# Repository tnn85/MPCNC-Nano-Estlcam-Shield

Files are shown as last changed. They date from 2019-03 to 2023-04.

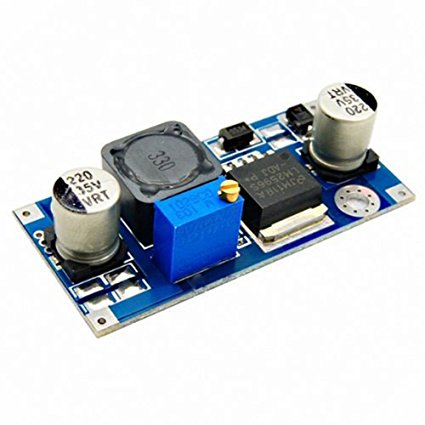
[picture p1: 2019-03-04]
Parts/Voltage Regulator/LM2596 Step Down Module.jpg

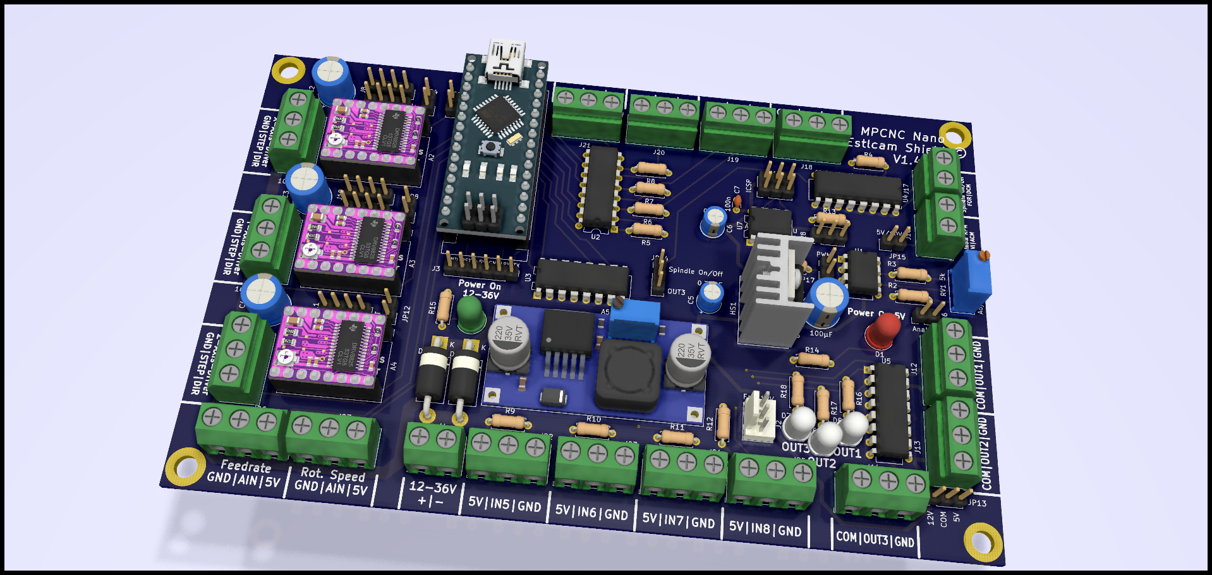
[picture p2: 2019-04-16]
Docs/Pics/V1.4/3D View/MPCNC Nano Estlcam Shield V1.4 3D Model 1.png

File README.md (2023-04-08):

**<<<BITTE BEACHTEN: Die Platine darf ausdrücklich NUR für die private Verwendung hergestellt werden. Der Weiterverkauf sowohl gewerblich als auch privat (darunter fällt auch der der Verkauf als "gebraucht") ist nicht gestattet. D.h. bitte nicht aus ökonomischen Gründen mehrere Platinen bestellen und dann die übrigen Platinen auf Ebay/Ebay Kleinanzeigen/Amazon/Facebook oder anderen Handelsplattformen öffentlich/halböffentlich anbieten! Beachtet die Lizenzbedingungen am Ende dises Dokuments. Danke für dein/euer Verständnis.>>>**  

Falls Interesse an der Platine besteht und ihr diese nicht selbst fertigen (ätzen/fräsen) wollt oder könnt, bietet der Moderator der FB-Gruppe "Uncle Phil's Werkstatt" die Bausätze an. Ich habe **nur** ihm gestattet, die Platine anzubieten. Andere Bezugsquellen sind von mir nicht genehmigt.

# MPCNC-Nano-Estlcam-Shield
English: A CNC shield for the MPCNC in conjunction with Estlcam  
Deutsch: Ein CNC Shield für die MPCNC in Verbindung mit Estlcam

# Konzept:  
Das MPCNC Nano Esltcam Shield stellt eine CNC Steuerungssplatine für die MPCNC bereit, die Einsteigern eine kostengünstige, auf die CNC-Maschine (MPCNC) und Software (Estlcam) zugeschnittene Steuerung als Schnittstellenlösung zwischen Maschine und Estlcam anbietet.  Die Steuerung bietet mehr Funktionalität als vergleichbare Steuerungen (z. B. das bekannte GRBL 0.8 "CNC Shield V3"), auf die Schrittmotortreibermodule (A4988, DRV8825, etc) gesteckt werden können und stellt zusätzlich eine Erweiterungsmöglichkeit für genauere, leistungsähigere Schrittmotortreiber bereit.

# Name:

 ***"MPCNC Nano Estlcam Shield"***  
 * __"MPCNC"__: Richtet sich vorrangig (aber nicht nur) an Einsteiger in Thema CNC, die mit der MPCNC  anfangen wollen und somit direkt die Kompatibiliät erkennen  
 * __"Nano"__: Auf Arduino Nano basierend  
 * __"Estlcam"__: Ist für die Verwendung mit Estlcam als Steuerungs- und CAM-Software zugeschnitten  
 * __"Shield"__: Soll ausdrücken, dass es, wie bei der Terminologie von Arduino üblich, als Zusatzmodul/"Piggyback" zum Arduino fungieren soll.
 
# Technische Anforderungen:

* Unterstützt Estlcam Version 11 (GRBL oder andere Firmware kann nach entsprechender Konfiguration auch mit der Platine verwendet werden)
* Arduino Nano Support (Original oder Klon)
* Zweilagige Platine
* Nur THT-Bauteile (kein SMD-Löten erforderlich)
* Schraubklemmen oder Stiftleisten für Anschluss externer Komponenten
* Betrieb mit 12-36V
* Konfiguration über Jumper
* Verpolungsschutz Versorgungsanschluss 
* Steckplätze für Pololu Schrittmotortreibermodule DRV8825 + A4988. TMC21x0 sollte auch funktionieren, wurde noch nicht getestet. 
* Mikrostepping über Jumper für Aufstecktreiber einstellbar
* Serienschaltung von zwei Schrittmotoren für X- und Y-Achsen. Einzelner Motor über Jumper auch im Einzelbetrieb möglich.
* Anschlussmöglichkeit von externen Treibern für alle 3 Achsen (DIR, STEP/PUL, GND). Es können auch Servomotoren damit angesteuert werden.
* Lüfteranschluss 12V 
* 7(8) galvanisch getrennte Eingänge (für Eingang 6 muss die Diode auf dem Arduino entfernt werden)
* Ausreichend Eingänge für Endstops/Programmsteuerung/Werkzeuglängensensor/Tastplatte. Eingänge beliebig konfigurierbar.
* 2 Ausgänge für Relais/SSR/etc mit 5V/12V/Open Collector. Ausgänge können über Estlcam angesteuert werden.
* Signalisierrung der Eingänge/Ausgänge über LEDs möglich (für Ausgänge schon vorhanden, bei Eingängen in Reihe schaltbar) 
* Spindel ON/OFF (galvanisch getrennt) +  Drehzahl (PWM / 0-5V / 0-10V) Ausgänge
* 2 analoge Eingänge Drehzahl + Vorschubanpassung
* optional erweiterbar durch ATTiny µC (greift Drehzahlsignal ab) 
* Testpunkte für Fehlersuche

# Optionale Anforderungen:

* Erweiterung um Handradsteuerung (vorraussichtlich nicht möglich, da Estlcam-seitig unterbunden)
* Drehzahlsteuerung von Spindeln/Fräsmotoren ohne FU über µC ATTiny
* Temperaturabhängige Lüfterreglung über PWM mit Temperaturalarm
* Absaugautomatik mit Nachlaufverzögerung 
* Auto Square
* Sicherung für Treiber
* Unterstützung für Trinamic SilentStepStick TMC2100/2130/2208/5160 (Konfiguration über Tristate-Jumper, Seriell, SPI) 
* Anschlussmöglichkeit für Bluetoothmodul (Übertragung von Estlcam über virtuelle serielle Schnittstelle)

# Ordnerstruktur:

* KiCad-Projektdatei
* Schematic (*.sch)
* PCB Layout (*.kicad_pcb)
* Netzliste (*.net)
* Firmware (Ordner für Firmware für Mikrocontroller)
* Enclosure (Ordner für Gehäuse-CAD-Dateien, STL-Dateien, Stecker)
* Docs (Ordner für Anleitung, Berechnungen, Verkabelungsbeispiele, Technisches Datenblatt, etc)
* Parts (Ordner für Datenblätter, Bill of Materials, Lieferanten, etc)
* Libraries (Ordner für projektspezifische Bauteilsymbole und Footprints)
* Readme 
* License

# Lizenz:
* Creative Commons CC-BY-SA-NC 4.0 License
* Created and Copyright by T.Nenz - E-Mail: MPCNCShield(at)outlook.de

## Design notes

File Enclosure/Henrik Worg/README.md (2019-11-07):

Till Front.stl fits directly on Daniels's housing.

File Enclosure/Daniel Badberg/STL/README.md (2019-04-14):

Ersteller:	Daniel Badberg
Datum:		13.04.2019
Lizenz:		Attribution-NonCommercial 3.0 (https://creativecommons.org/licenses/by-nc/3.0/)

STL Dateien zum drucken mit eurem 3D-Drucker.

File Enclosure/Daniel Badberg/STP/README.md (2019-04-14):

Ersteller:	Daniel Badberg
Datum:		13.04.2019
Lizenz:		Attribution-NonCommercial 3.0 (https://creativecommons.org/licenses/by-nc/3.0/)

STP Dateien zum weiterverarbeiten, z.B. mit Fusion 360 oder anderen CAD-Programmen.

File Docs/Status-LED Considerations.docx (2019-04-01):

Wie sieht es mit LEDs an den Eingängen / Ausgängen aus ("Status LED"). Sollten welche vorgesehen werden? In der Software wird es mir zwar signalisiert, aber ein Option in Hardware hat auch Vorteile (unter anderem zur Fehlersuche ohne Software).

Es gibt ja folgende Möglichkeiten der Schaltung:
Für Eingänge (Annahme, dass Status LED immer funktioniert):

1. Status LED aus Sicht des Eingangs vor den Optokoppler in Reihe zu der LED im Optokoppler
  - Vorteil:
    - Strombegrenzung ist durch Widerstand schon vorhanden (müsste auf den Wert für 2 LEDs angepasst werden)
    - Defekte LED im Optokoppler wird erkannt, falls man weiß, dass die Status LED funktioniert.
  - Nachteil:
    - Defekter Phototransistor im Optokoppler wird nicht erkannt. Es kann an diesem oder am Eingang des Arduino µC liegen.
    - Status LED ist zwingend zu bestücken oder es muss eine Lötbrücke gesetzt werden.
    - Kann auch schon unabhängig von der Platine extern so beschaltet werden (Also LED in Leitung mit Sensorschalter)
2. Status LED aus Sicht des Eingangs vor den Optokoppler parallel zur LED im Optokoppler
  - Vorteil:
    - Muss nicht zwingend bestückt werden.
  - Nachteil:
    - Defekte LED im Optokoppler wird nicht erkannt. Es kann an allen Komponenten hinter der Status LED liegen, dass Eingang softwareseitig nicht toggelt.
    - Zusätzlicher Vorwiderstand notwendig
    - Kann auch schon unabhängig von der Platine extern so beschaltet werden (Also LED mit Vorwiderstand z.b. mit Kabel zwischen Ex und GND)
3. Status LED aus Sicht des Eingangs hinter den Optokoppler. Anode an µC-Eingangspin, Kathode an Collector-Anschluss des Phototransistors vom Optokoppler
  - Vorteil:
    - Strombegrenzung durch Pullup-Widerstand im Arduino µC. Kein zusätzlicher Vorwiderstand notwendig.
  - Nachteil:
    - Keine Ortung bei Defekt möglich. Es kann µC Eingang oder Optokoppler (LED oder Transistor sein). Man weiß nur, ob alles funktioniert oder etwas nicht funktioniert.
4. Status LED aus Sicht des Eingangs hinter den Optokoppler. Anode an 5V, Kathode der Status LED an Vorwiderstand, anderer Anschuss des Vorwiderstand an Collector-Anschluss des Phototransistors vom Optokoppler bzw. den µC-Eingangspin (Bei Aktivierung wird dieses Signal auf GND gezogen und die Status LED leuchtet.
  - Vorteil: Fehlerursache auf Optokoppler bzw µC Eingang eingrenzbar (Wenn Status LED bei Aktivierung leuchtet, ist der Optokoppler i. O.)
    - Fehlerursache auf Optokoppler bzw µC Eingang eingrenzbar (Wenn Status LED bei Aktivierung leuchtet, ist der Optokoppler i. O.)
  - Nachteil:
    - Zusätzlicher Vorwiderstand notwendig.

Für Ausgänge (Annahme, dass Status LED immer funktioniert):
Hier ergibt für mich eigentlich nur eine Status LED vor den Ausgangstreiber an den Ausgang des µC Sinn, da hier das Spannungslevel gleich bleibt (im Gegensatz zum (5V, 12V oder Open Collector Ausgang des Relaistreibers ULN2003A).
Dann natürlich wieder mit Vorwiderstand gegen GND (leuchtet bei Aktivierung). Bei 2 digitalen Ausgängen sollte die Strombelastung für den µC auch nicht all zu hoch sein, wenn dann die Ausgänge des µC die LEDs speisen müssen.
In Reihe der Ausgänge hinter die Treiber geht nicht, wegen dem Strom, der für Relais hoch sein muss.
Parallel zu der den Ausgängen (zwischen COM und den einzelnen Ausgängen) würde bedeuten, dass man den Vorwiderstand (falls er denn fest beschrieben ist) am höchsten Spannungslevel ausrichten muss und dadurch die LED bei kleinen Spannungen nur mit relativ geringem Strom betrieben wird. Außerdem gilt auch hier: An den Ausgang kann jeder noch selbst parallel eine LED mit Vorwiderstand extern schalten.

Hab ich irgendwo einen Denkfehler? Es gibt so viele Möglichkeiten, da dreht sich der Kopf bei mir.

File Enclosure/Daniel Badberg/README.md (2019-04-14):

**Ersteller:	Daniel Badberg**  
**Datum:		13.04.2019**  
**Lizenz:		Attribution-NonCommercial 3.0 (https://creativecommons.org/licenses/by-nc/3.0/)**

Gehäuse zum Drucken mit einem 3D-Drucker für das neue ***MPCNC Nano Estlcam Shield*** von T.Nenz. 
Das Projekt ist in der Facebook-Gruppe von Uncle Phil (https://www.facebook.com/groups/722641598074003/) enststanden. 
Die Platine bekommt Ihr auf Email-Anfrage bei **MPCNCShield(at)outlook.de** von T.Nenz, das Gehäuse inkl. der FreeCAD und Step-Dateien gibt es hier.

Viel Spaß beim Nachbauen.

Hier gibt es ein kleines Assembly Video dazu: https://youtu.be/D2-taHU4rp4
Das Video ist auch in diesem Repositorium verfügbar.

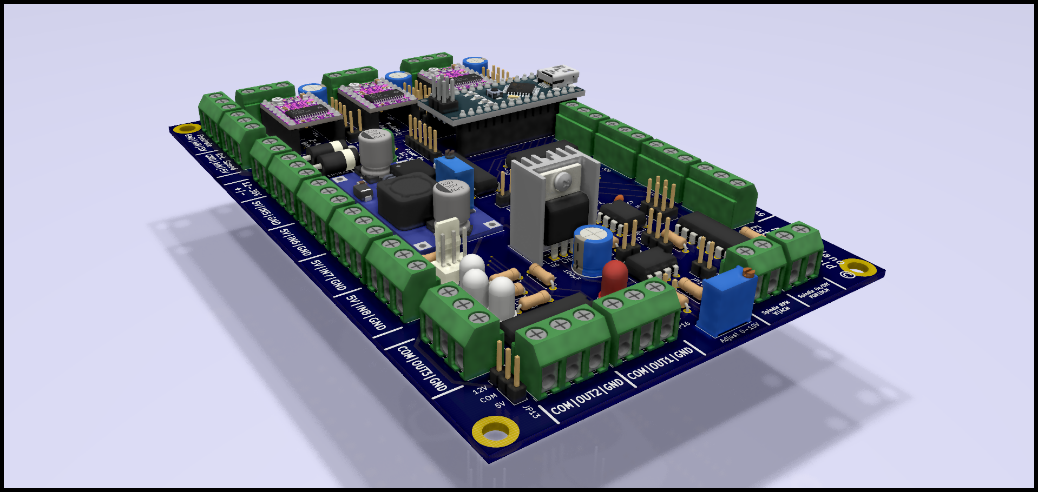
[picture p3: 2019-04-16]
Docs/Pics/V1.4/3D View/MPCNC Nano Estlcam Shield V1.4 3D Model 2.png

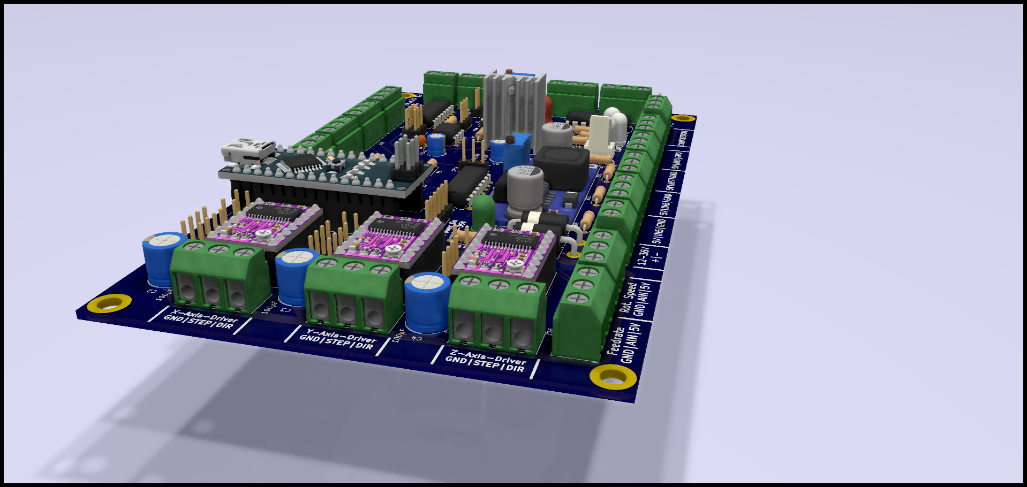
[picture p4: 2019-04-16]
Docs/Pics/V1.4/3D View/MPCNC Nano Estlcam Shield V1.4 3D Model 3.png

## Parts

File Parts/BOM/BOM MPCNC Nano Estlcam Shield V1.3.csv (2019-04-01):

ID | Bezeichner | Gehäuse | Stückzahl | Bezeichnung | Anbieter und Referenz
1 | U6 | TO-220-3_Vertical | 1 | L7805
2 | C6 | CP_Radial_D5.0mm_P2.00mm | 1 | 0,1µF
3 | C5 | CP_Radial_D5.0mm_P2.00mm | 1 | 0,33µF
4 | C7 | C_Disc_D3.0mm_W1.6mm_P2.50mm | 1 | 100n
5 | A5 | LM2596_Step_Down_Module-21.3x43.6mm | 1 | LM2596_Step_Down_Module
6 | H3,H1,H2,H4 | MountingHole_4.3mm_M4_DIN965_Pad | 4 | MountingHole
7 | R7,R8,R12,R4,R5,R6,R9,R11,R14,R10 | R_Axial_DIN0207_L6.3mm_D2.5mm_P7.62mm_Horizontal | 10 | 220
8 | C1,C3,C4,C2 | CP_Radial_D8.0mm_P3.50mm | 4 | 100µF
9 | U5 | DIP-16_W7.62mm | 1 | ULN2003
10 | U2,U3,U4 | DIP-16_W7.62mm | 3 | LTV-847
11 | U7 | DIP-8_W7.62mm | 1 | ATtiny45-20PU
12 | U1 | DIP-8_W7.62mm | 1 | LM358
13 | D2,D3 | D_DO-201AD_P15.24mm_Horizontal | 2 | 1N5822
14 | R2,R13,R3 | R_Axial_DIN0207_L6.3mm_D2.5mm_P7.62mm_Horizontal | 3 | 10k
15 | R1,R16,R17,R18 | R_Axial_DIN0207_L6.3mm_D2.5mm_P7.62mm_Horizontal | 4 | 1k
16 | R15 | R_Axial_DIN0207_L6.3mm_D2.5mm_P7.62mm_Horizontal | 1 | 1.8k
17 | RV1 | Potentiometer_Bourns_3296W_Vertical | 1 | 5k
18 | A1 | Arduino_Nano | 1 | Arduino Nano
19 | A4,A3,A2 | Pololu_Breakout-16_15.2x20.3mm | 3 | Pololu_Breakout_DRV8825
20 | J27,J22,J13,J14,J12,J21,J18,J19,J20,J24,J25,J4,J5,J6,J23,J26 | TerminalBlock_RND_205-00013_1x03_P5.00mm_Horizontal | 16 | Screw_Terminal_01x03
21 | HS1 | Heatsink_China_TO220_(22x)15x10mm_1xDrill1.5mm | 1 | Heatsink 7805
22 | J17,J16,J1 | TerminalBlock_RND_205-00012_1x02_P5.00mm_Horizontal | 3 | Screw_Terminal_01x02
23 | D7,D6,D5 | LED_D5.0mm | 3 | LED TRANSPARENT
24 | D4 | LED_D5.0mm | 1 | LED RED
25 | D1 | LED_D5.0mm | 1 | LED GREEN
26 | J29 | PinHeader_1x02_P2.54mm_Vertical | 1 | Conn_01x02_Male |  | Ersetzt durch PinHeader_1x20_P2.54mm_Vertical
27 | J28 | PinHeader_1x03_P2.54mm_Vertical | 1 | Conn_01x03_Male |  | Ersetzt durch PinHeader_1x20_P2.54mm_Vertical
28 | J15 | PinHeader_2x03_P2.54mm_Vertical | 1 | Conn_02x03_Odd_Even |  | Ersetzt durch PinHeader_1x20_P2.54mm_Vertical
29 | J3 | PinHeader_1x06_P2.54mm_Vertical | 1 | Conn_01x06_Male |  | Ersetzt durch PinHeader_1x20_P2.54mm_Vertical
30 | JP2,JP16,JP17,JP3,JP8,JP10,JP5,JP15,JP11,JP7,JP6,JP9,JP12,JP4,JP1 | PinHeader_1x02_P2.54mm_Vertical | 15 | Jumper_NO_Small |  | Ersetzt durch PinHeader_1x20_P2.54mm_Vertical
31 | JP14,JP13 | PinHeader_1x03_P2.54mm_Vertical | 2 | Jumper_3_Open |  | Ersetzt durch PinHeader_1x20_P2.54mm_Vertical
32 | J2 | Molex_KK-254_AE-6410-03A_1x03_P2.54mm_Vertical | 1 | Conn_01x03_Male
33 | J8,J7,J11,J10,J9 | PinHeader_1x04_P2.54mm_Vertical | 5 | Conn_01x04_Male |  | Ersetzt durch PinHeader_1x20_P2.54mm_Vertical
34 | A4,A3,A2 | PinSocket_1x08_P2.54mm_Vertical | 6 | Conn_01x08_Female
35 | A1 | PinSocket_1x15_P2.54mm_Vertical | 2 | Conn_01x08_Female
36 | JPxx | Jumper | 20 | Jumper
37 | Jxx | PinHeader_1x20_P2.54mm_Vertical | 4
38 | HS1 | Schraube M3x6mm | 1

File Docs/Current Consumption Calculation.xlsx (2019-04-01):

Component | Function | Quantity | Voltage [V] | Current (avg) [mA] | Current (peak) [mA]
RC Servo | Control external triac potentiometer | 1 | 5 | 400 | 550
Optocoupler LTV847 Channel | Input Isolation for µC | 9 | 5 | 5
Arduino Nano |  | 1 | 5 | 200 | 300
Darlington Transistor ULN2003A Channel Input | Relay Driver for high coil currents | 3 | 5 | 0.5
Darlington Transistor ULN2003A Channel Output | Relay Driver for high coil currents | 3 | 12 | 200 | 500
Fan | Housing fan for cooling PCB | 1 | 12 | 260 | 450
Relay (electromechanical) |  | 2 | 12 | 104

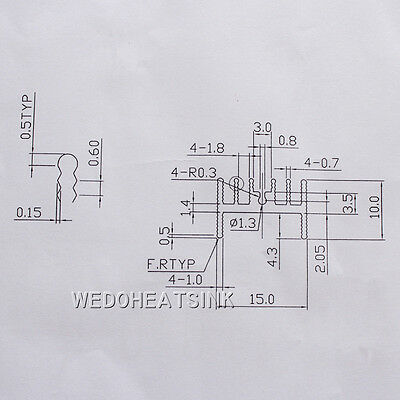
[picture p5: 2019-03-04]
Parts/Heatsink/Heatsink 7805 Drawing.jpg

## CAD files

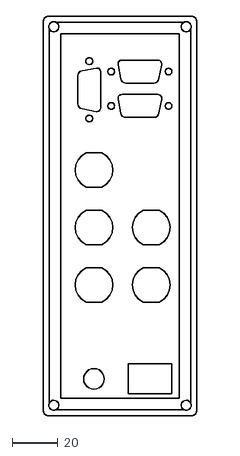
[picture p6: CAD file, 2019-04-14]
Enclosure/Daniel Badberg/DXF/Frontplatte.dxf
66.7 x 174.0

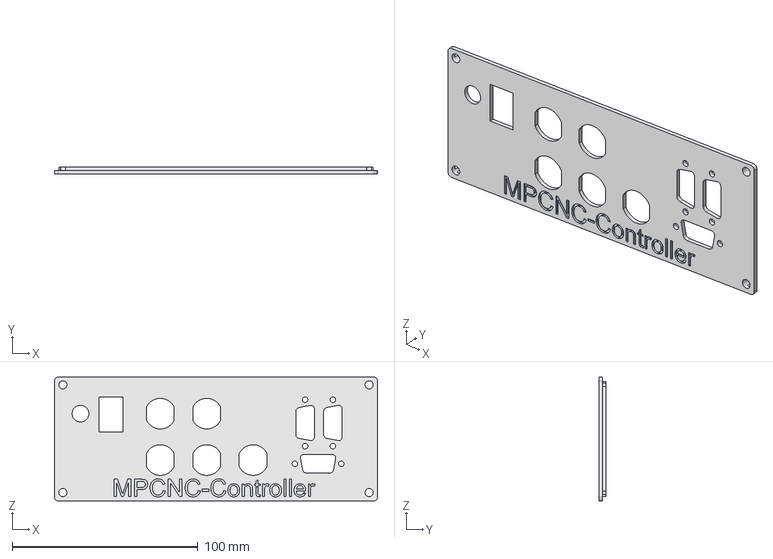
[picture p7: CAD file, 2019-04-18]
Enclosure/Daniel Badberg/MPCNC-Frontplatte.FCStd
174.0 x 4.00 x 66.7 mm

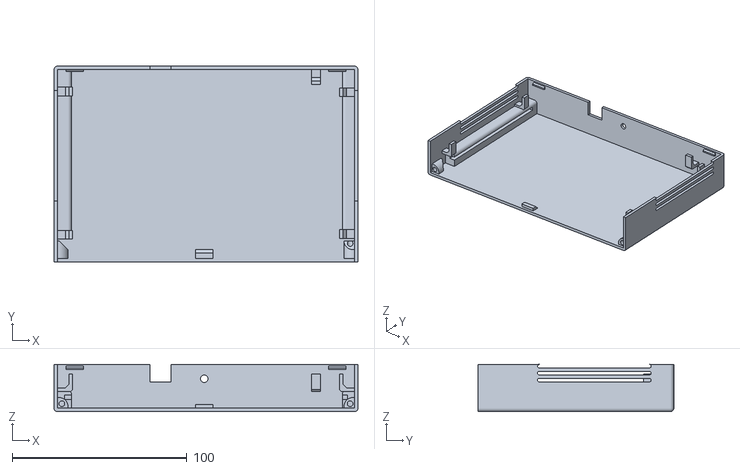
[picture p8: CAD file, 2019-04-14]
Enclosure/Daniel Badberg/STL/Unterteil.stl
174.0 x 112.0 x 27.0

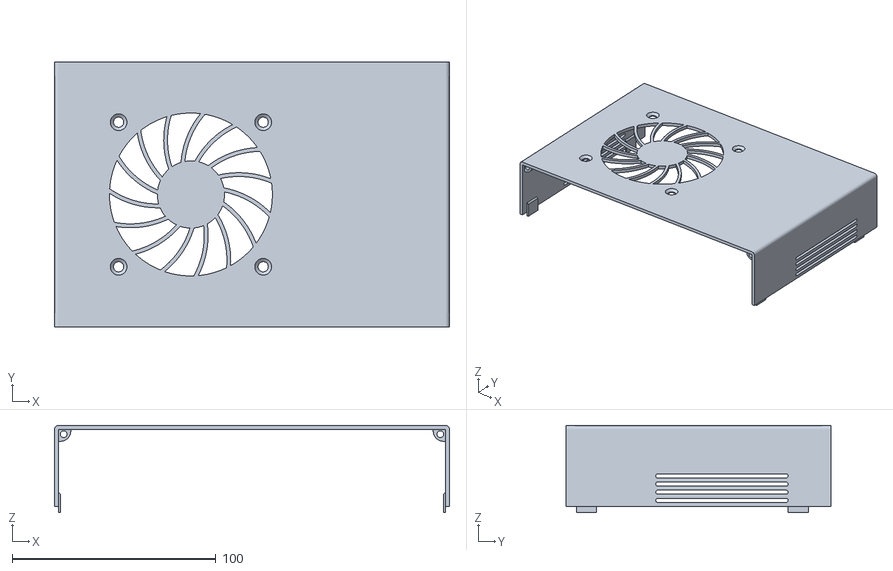
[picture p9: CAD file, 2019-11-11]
Enclosure/Henrik Worg/Tillbox groß/Oberteil Nano Controller Box.stl
194.0 x 130.0 x 42.8

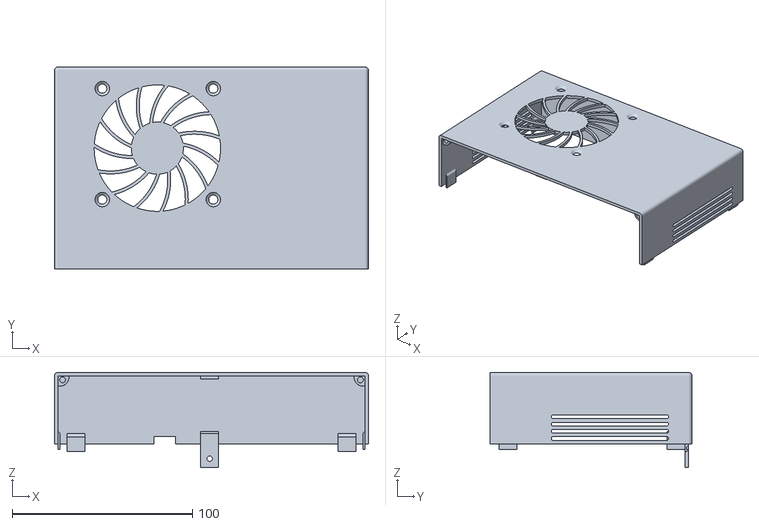
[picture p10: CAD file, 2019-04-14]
Enclosure/Daniel Badberg/STL/Oberteil-70mm-Luefter.stl
174.0 x 112.0 x 52.9

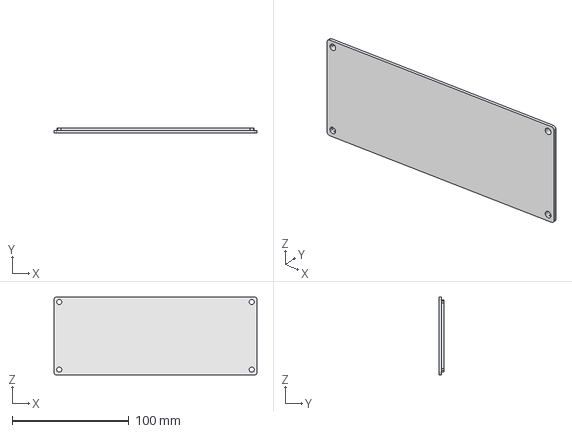
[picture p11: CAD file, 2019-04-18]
Enclosure/Daniel Badberg/STP/Frontplatte-Blanko-korrigiert1.step
174.0 x 4.00 x 66.7 mm

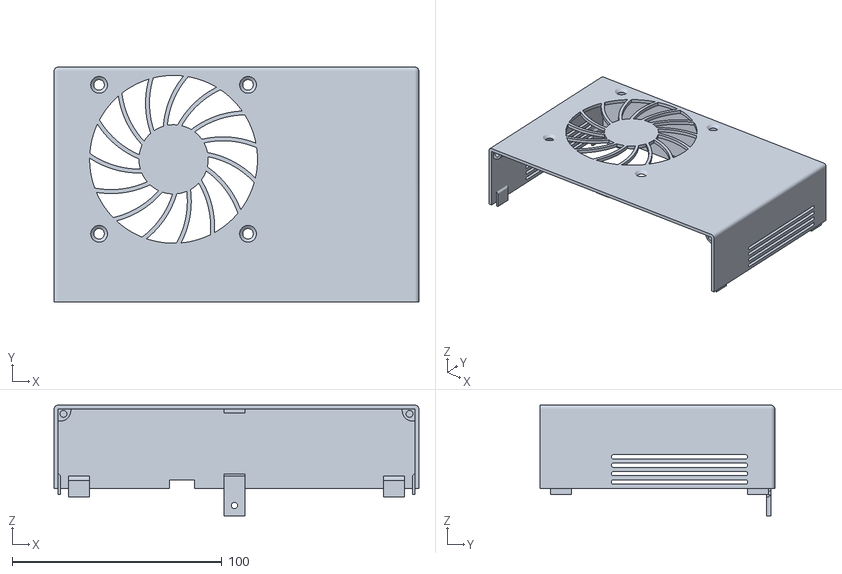
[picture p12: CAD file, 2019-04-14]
Enclosure/Daniel Badberg/STL/Oberteil-80mm-Luefter.stl
174.0 x 112.0 x 52.9

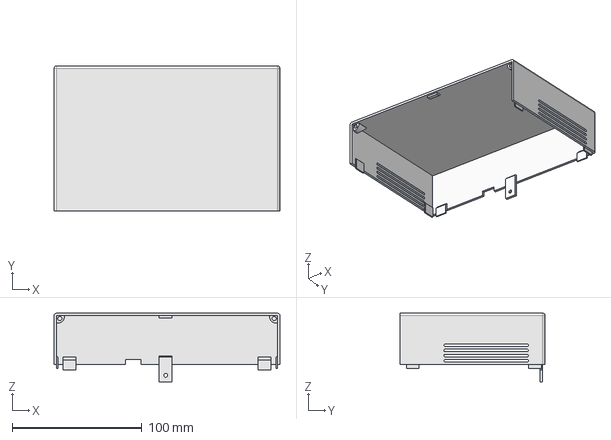
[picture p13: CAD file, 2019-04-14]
Enclosure/Daniel Badberg/STP/Oberteil-Blanko.step
174.0 x 112.0 x 52.9 mm

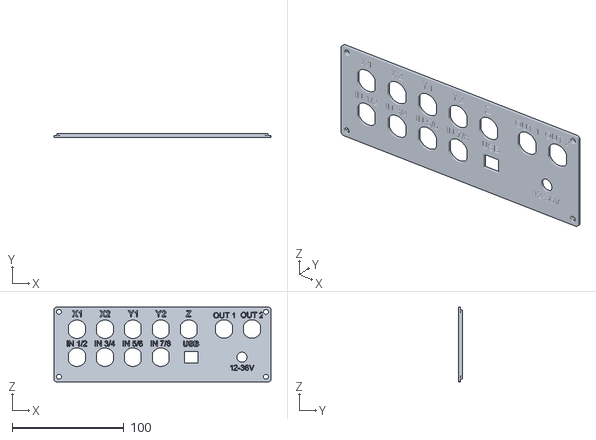
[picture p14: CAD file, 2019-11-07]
Enclosure/Henrik Worg/Tillbox groß/Rückseite groß.stl
194.0 x 4.00 x 66.7

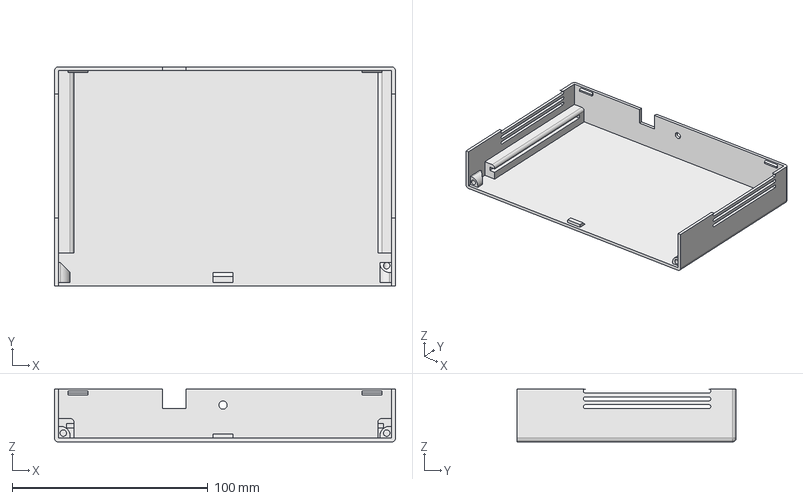
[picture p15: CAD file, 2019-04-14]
Enclosure/Daniel Badberg/STP/Unterteil-Blanko.step
174.0 x 112.0 x 27.0 mm

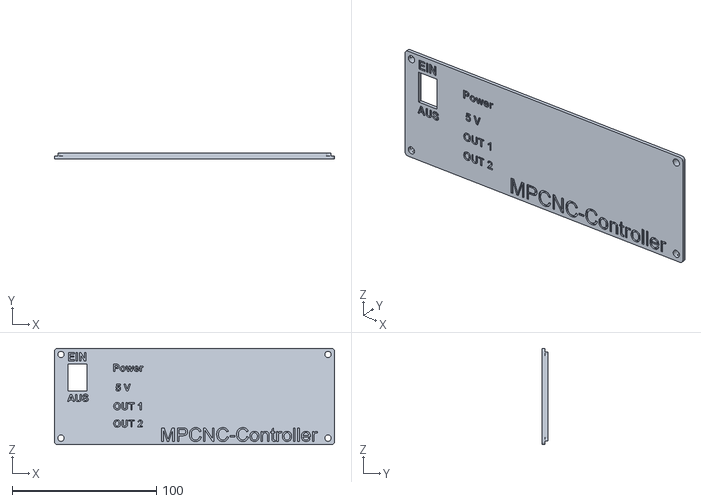
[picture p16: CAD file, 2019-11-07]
Enclosure/Henrik Worg/Tillbox groß/Front groß.stl
194.0 x 4.00 x 66.7

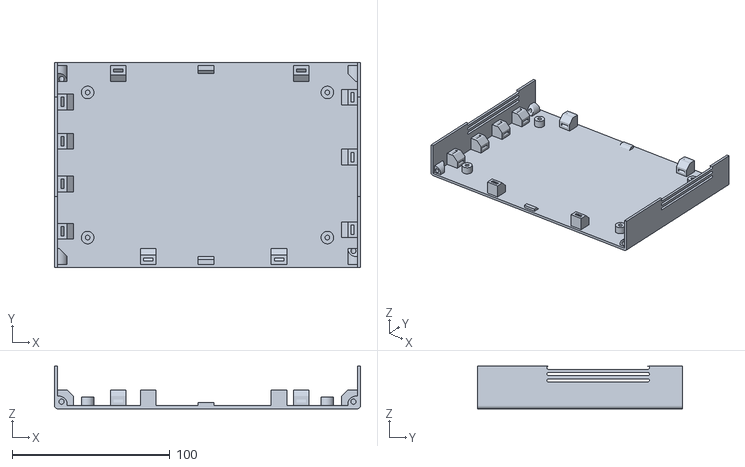
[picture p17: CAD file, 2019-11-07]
Enclosure/Henrik Worg/Tillbox groß/Unterteil groß.stl
194.0 x 130.0 x 27.0

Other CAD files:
Enclosure/Daniel Badberg/STP/Frontplatte-Komplett-korrigiert1.step
Enclosure/Henrik Worg/Till Front.stl
Enclosure/Henrik Worg/Tillbox groß/Oberteil groß.stl
Enclosure/Daniel Badberg/STL/Frontplatte-Blanko-korrigiert1.stl
Enclosure/Daniel Badberg/STL/Frontplatte-komplett-korrigiert1.stl

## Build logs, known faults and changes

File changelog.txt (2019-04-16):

- Version 1.4 of MPCNC Nano Estlcam Shield   
   PCB schematic changes:
    # Changed LED colours (D1:red, D4:green, D5-7:Clear/red)
   PCB layout changes:
    + Footprints for LEDs added to project footprint library ("MPCNC_Shield_Footprints"). 
    # Changed footprint of LEDs 
    # Moved silk screen reference fo L7805 (U6). Reference was hidden by heatsink
    + Added LED 3D models to footprint. LEDs show correct color for 3D model (green, red, white[clear])
    # Changed 3D model for potentiometer (KiCAD standard library model now available in latest KiCAD release 5.10)
    # Changed 3D model for screw terminal blocks (J1; J4-6; J12-14; J16-J17; J18-27)

- Version 1.3 of MPCNC Nano Estlcam Shield   
   PCB schematic changes:
    # Changed electrolytic capacitor values for L7805 (0,33µF + 0,1µF)
   PCB layout changes:
    # Changed footprint of electrolytic capacitor for L7805 (D=8mm/RM=3,5mm -> D=5mm/RM=2,0mm)
    # Revised heatsink footprint
    + Footprints for many components added to project footprint library ("MPCNC_Shield_Footprints"). Modified footprints from standard KiCad library with value on 
silkscreen
    + Added "Uncle Phil" logo on backside silk screen layer
    + Added jumper function description on frontside silk screen layer
    # Changed mounting holes (Edge.cut layer -> footprint)

- Version 1.2 of MPCNC Nano Estlcam Shield   
   PCB schematic changes:
    + Power LEDs (5mm LED) added(5V and VMot[formerly VDD])
    + 3,3V connector added
    + Output Enabled LEDs added (3 x 3mm LED + 1k resistor for OUT1,2,3), Pulls down ouput signal on startup 
    # Replaced powerflag "VDD" with "VMot" (new custom symbol)
    + Added net names for Microstepping jumper
    # Signal "Analog_0_5V" now connected to "LM358 +"-Pin net (after instead of before LP-filter)
    # Replaced servo connector symbol (Conn_01x03_Female to Conn_01x03_Male)
    # Mirrored Microstepping and FLT jumper (Pin 1:5V, Pin 2:Signal)
    # Changed net names ("Ex"-> "INx", "Ax" -> "OUTx") 
   PCB layout changes:
    # Silk screen text input/output description corrected ("Feedrate" and "E5")
    # Changed silk screen text language to English ("Ex"-> "INx", "Ax" -> "OUTx") 
    # Moved traces and parts for schematic changes and increased margin
    # Added silk screen text for some parts (Arduino Nano, LM2596 step down module, Driver modules, Microstepping Jumper, Fan, 0-10V Adjustment Poti and LEDs)
    # Revised LM2596 module footprint
    # Replaced RV1 Trimmer/Potentiometer Footprint (Potentiometer_Bourns_3296Y_Vertical -> Potentiometer_Bourns_3296W_Vertical). Footprint (2 Pads) of Potentiometer_Bourns_3296Y_Vertical is still on PCB. -> It is possible to mount either potentiometer.
    # Changed TerminalBlocks footprint and pin pitch (5.08mm -> 5.00mm)
   Library:
    + Added power flag "VMot"
    # Renamed "DCDC_LM2596_Step_Down_Module" to "LM2596_Step_Down_Module"
    + Added modified footprints from KiCAD standard library for some components (Arduino Nano, Terminal blocks, Pololu driver breakout board, Bourns 3296W potentiomter, Heatsink for L7805) (added 3D models to footprint. However, 3D models are not published in repository for licensing reasons)
-----------------------------------------------------------------------------

- Version 1.1 of MPCNC Nano Estlcam Shield
   PCB schematic changes:
    #  Symbol value removed (default symbol value for BOM creation)
    + Added field value "Funktion" to all symbols for part description
    # Symbol reference annotation changed
    + 12-36V power supply capability (with LM2596 Step Down Module)
    + Support for Triac Servo (with ATtiny µC)
     - Removed Output A4 (PWM)
    + Serial stepper motor connection (2 Stepper in series) for X- and Y- Axis possible
    + Added Heatsink for LM7805 5V voltage regulator

   PCB layout changes:
    # Complete PCB layout change
    +PCB layout intended for silk screen on PCB board edges

- New project folder structure
- Added custom libraries (Footprint and Symbols)

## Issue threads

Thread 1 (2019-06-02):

MPCNC Shield Attiny45-20PU

Multi94, 2019-06-02:
Hallo,
ich habe das Shield hier gefunden und nach einiger Überlegung die Platine machen lassen. Die Bauteile sind auch schon bestellt zum bestücken.Nun ist mir aber eine Frage aufgekommen und zwar wird auf der Platine auch ein Attiny45-20PU verbaut mit welchem Sketch oder Programm muss dieser bespielt werden das konnte ich bis jetzt leider nicht finden. Der Nano wird ja über Estlcam Programmiert nur der Tiny ist mir nicht klar. Ich hoffe es kann mir da einer weiterhelfen.

Mfg und vielen dank für das geniale Shield.

Hello,
I found the shield here and, after some deliberation, had the board made. The components are already ordered to equip. But I have come up with a question and although on the board also an Attiny45-20PU installed with which sketch or program this must be recorded I could not find so far unfortunately. The Nano is indeed programmed via Estlcam only the Tiny is not clear to me. I hope someone can help me there.

Mfg and thank you for the brilliant shield.

duke2421, 2019-06-02:
Der Attiny ist für eigene Erweiterungen gedacht. Für die eigentliche Funktion des Boards wird er nicht benötigt.

Multi94, 2019-06-06:
Danke für die schnelle Antwort. Gibt es dazu Irgendwo bei spiele die man sich ansehen kann oder noch nicht.

Eine frage hätte ich noch und zwar gibt es bei den Stepper Treiber verschiedene Jumper einmal mit FLT JP8 JP4 JP12 und einmal den Jumper JP29 was kann ich damit einstellen und gibt es Irgendwo eine Anleitung was die Jumper machen da ich nicht jeden auf dem Board nachvollziehen kann leider.

Danke im voraus.

tnn85, 2020-03-15:
Die FLT Jumper JP4, JP8 und JP12 sind für diese Art von Pololu-Schrittmotortreiberplatinen gedacht. Da gibt es mehrere verschiedene, die auf unterschiedlichen Chips basieren z.b den DRV8825 oder den A4988. Der A4988 braucht 5V und deswegen muss bei diesem der Jumper gesetzt werden. Beim DRV8825 ist das nicht notwendig und deshalb kann der Jumper frei bleiben. Über den Pin des Jumpers, der mit dem Treiber verbunden ist, kann ein Fehlerfall des Chips erkannt werden.

JP29 gibt es nicht. Es gibt den J29 Anschluss und bietet nur eine Anschlussmöglichkeit an das 3,3V Potential des Arduino Nano.

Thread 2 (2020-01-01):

Bauteile

bresam, 2020-01-01:
Gibt es eine übersichtliche und detaillierte Teile- / Stückliste der verbauten Bauteile?

MrUrdam, 2020-01-01:
Am einfachsten mal in dieser Gruppe vorbei schauen. https://m.facebook.com/groups/722641598074003/?ref=group_header&view=group

Dort gibt es viel Support zu diesem Projekt. Teilelisten. Ab und zu auch Sammelbestellungen der Teile. Usw.

bresam, 2020-01-01:
> Am einfachsten mal in dieser Gruppe vorbei schauen. https://m.facebook.com/groups/722641598074003/?ref=group_header&view=group
>
> Dort gibt es viel Support zu diesem Projekt. Teilelisten. Ab und zu auch Sammelbestellungen der Teile. Usw.

Vielen Dank soweit, habe mir nun mal nen FB-Fake-Account angeschaft. Is ja ned jeder bei Facebook dabei ;-)

MrUrdam, 2020-01-01:
Das ist natürlich klar. Aber für das Thema MPCNC und auch speziell zu diesem Board lohnt es sich.
Dort findet man auch ein passendes Gehäuse und  bekommt sehr viele hilfreiche Tipps.

Leider ist der Entwickler des Boards seit einem halben Jahr inaktiv aber in der Gruppe hat sich viel Wissen angehäuft.

Der UnclePhil ist ein Youtuber, welcher durch die MPCNC viele neue Abonnenten gewinnen konnte. Er plant für 2020 auch eine weiter CNC für den Hobbybereich.

bresam, 2020-01-01:
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

Ja ich folge UnclePhil schon länger und bin durch Ihn damals auf das MPCNC Projekt gestossen und dann natürlich auch auf das Till-Board.

Ist nur schade, dass man sich die Informationen etwas mühsam zusammenkratzen muss. Nichmal auf der Seite von UnclePhil finde ich ne sinnvolle Teileliste :-( Werde dann hier wohl nen Pull-Request machen, wenn ich die Liste zusammenhabe ;-)

sboettger, 2020-01-24:
Die BOM ist doch da: Parts/BOM/BOM MPCNC Nano Estlcam Shield V1.3.csv

UliSchirm, 2020-01-27:
Hallo Sebastian,

erst mal herzlichen Dank fürs Entwickeln und Teilen des MPCNC-Nano-Estlcam-Shield, ich bin begeistert!

Sehr gerne wollte ich mich an der Sammelbestellung beteiligen (siehe unten). Leider hatte ich bislang keinen Facebook-Account und mir eigens dafür einen angelegt, um die Inhalte der Facebook-Gruppe sehen zu können. Aus Gründen, die ich nicht nachvollziehen kann, wurde jedoch mein Facebook Account nach kurzer Zeit gesperrt und es ist mir trotz unterschiedlichster Maßnahmen nicht gelungen, ihn zu reaktivieren.

Nun möchte ich gerne anfragen, ob die Sammelbestellung noch läuft und ob es eine Möglichkeit gibt, sich ohne Facebook Account daran zu beteiligen. Dafür wäre ich ausgesprochen dankbar.

Herzliche Grüße,
Ulrich Schirm

Panoramastr. 133
72766 Reutlingen

Telefon 07121/6968747
Mobil 0172/7157799
ulrich.schirm@icloud.com

Anfang der weitergeleiteten Nachricht:

Von: Google Formulare <forms-receipts-noreply@google.com>
Betreff: MPCNC-NANO-CONTROLLER
Datum: 18. November 2019 um 08:09:02 MEZ
An: ulrich.schirm@gmx.de

Danke, dass Sie das Formular MPCNC-NANO-CONTROLLER <https://docs.google.com/forms/d/e/1FAIpQLScrkrBjcatyCYAV6Yj0laAVntHfSL6jYRiq54oJQRNFE4qF_Q/viewform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> ausgefüllt haben
Wir haben folgende Informationen von Ihnen erhalten:
ANTWORT BEARBEITEN <https://docs.google.com/forms/d/e/1FAIpQLScrkrBjcatyCYAV6Yj0laAVntHfSL6jYRiq54oJQRNFE4qF_Q/viewform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>
MPCNC-NANO-CONTROLLER

Hier ist der original-Post aus FaceBook zu finden
https://www.facebook.com/groups/722641598074003/permalink/962685577402936/ <https://www.google.com/url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>

Deine eMail wird nicht an Dritte weitergegeben!! Nur zur Kontaktaufnahme dieser Anfrage!!

E-Mail-Adresse *
 ulrich.schirm@gmx.de
FaceBook Name *
 Ulrich Schirm

Vorname Name *
 Ulrich Schirm

Strasse *
 Panoramastr. 133

PLZ *
 72766

Ort *
 Reutlingen

Anzahl Basisset zu je 32€: *
(Platine + aufzulötende Bauteile)
0
1
2
3
4
5
6
7
8
9
10

Anzahl Zusatzsets zu je 12€: *
(1 Arduino Nano + 1 Spannungswandler LM2596 + 3 Steppertreiber DRV8825)
0
1
2
3
4
5
6
7
8
9
10

Versandoptionen *
Wähle deine gewünschte Versandart
  Porto + Verpackung Deutschland: 6€
 Porto + Verpackung Österreich: 10€
 Porto + Verpackung Schweiz: 17€

DHL Sendungsverfolgung *
Ich bin mit der Weitergabe meiner Email-Adresse an DHL zur Sendungsverfolgung einverstanden.
  JA
 NEIN

Eigenes Google-Formular erstellen <https://docs.google.com/forms?usp=mail_form_link>

McMakeIT, 2020-05-20:
Hallo, ich greife den Issue hier noch mal auf. Auch ich bin einer der Sorte ohne Facebook-Account (ja, das ist bewusst so gewollt) und würde gerne auch in den Genuss von Platinen kommen. Mein Vorschlag wäre eine Sammelbestellung über diesen Issue zu tätigen und tracken. Natürlich nur zum Selbstkostenpreis z.B. bei https://portal.multi-circuit-boards.eu/ plus ggf. Versand. @tnn85: Wäre das für den Urheber OK? Grüße; Oliver

RalfGaiser, 2020-05-23:
Hallo Oliver, da würde ich sofort zugreifen und das Angebot annehmen wollen. Sofern Uncle Phil und die Entwickler des Boards nichts dagegen haben, würde ich die Platine und die Bauteile gerne von dir beziehen. Entweder Zusbau oder bereits fertig verlötet, ist mir „wurscht“ :-)
Ginge das? Kannst dich ja mal melden, wegen des weiteren Ablaufs.
Lieben Dank und Gruss, Ralf

tnn85, 2020-05-23:
@McMakeIT @RalfGaiser Sorry, scheinbar funktionieren die GitHub Notifications nicht und ich wurde gerade erst auf eure Kommentare aufmerksam gemacht.
Zu dem Vorschlag von McMakeIT: Ich hab grundsätzlich nichts gegen Sammelbestellungen, aber die hier unter den Issues zu organisieren ist der falsche Ort.
Was ich auch nicht möchte ist, dass die Platinen in größerer Stückzahl irgendwo bestellt werden und dann der "Rest" ohne mein Wissen verkauft wird.
Der Gedanke war schon, dass man sich anhand der Gerber-Dateien sich seine Platine nur für sich selbst fräst oder ätzt.
Ich verstehe die Problematik nun überhaupt Sammelbestellungen organisieren zu können, aber ich hab gemerkt, dass in der Vergangenheit der Vertrieb der Platinen ohne mein Wissen wilde Auswüchse erreicht hat und ich deshalb das nun etwas strenger handhabe.
In der Facebook-Gruppe habe ich seit kurzem nur mit einem der Moderatoren die Abmachung, dass er die Platinen im Set mit den Bauteilen und meiner 50-seitigen Anleitung anbieten darf.  Wenn also Bedarf besteht, kann ich den Kontakt vermitteln. Meine Email-Adresse findet ihr ganz unten in der Readme.md.

McMakeIT, 2020-05-23:
@tnn85: Danke für die schnelle und ausführliche Antwort. Alles verständlich und nachvollziehbar. Aus diesem Grund hatte ich auch erst über den Issue angefragt und wollte keine Sammelbestellung starten.
Ich selbst kann keine Platine ätzen und fräsen. Eine Einzelbestellung halte ich nicht für wirtschaftlich. Dann wirst du die Tage mal Post von mir bekommen. Danke für das Angebot.

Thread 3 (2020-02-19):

Firmware Ordner?

isjo-org, 2020-02-19:
Hallo!

lt. Readme sollte es einen Firmware Ordner mit dem Code für den Arduino geben, habe ich etwas überlesen, oder übersehen?

Mir ist bekannt, dass es eine Facebook Gruppe gibt, jedoch bin ich strickter Social Media Gegner :/

Danke, lg

Skudderon, 2020-02-19:
Hallo,
der Arduino Nano wird durch Estlcam mit der entsprechenden Firmware geflasht.
Der Ordner ist für spätere (optionale) Firmware für den Attiny gedacht.

... eine Information die im Social Media bekannt ist ;)

VG
der Admin der Facebook Gruppe

isjo-org, 2020-02-19:
Danke!

Closed 2020-02-19.

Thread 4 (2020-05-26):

Trinamic Schrittmotortreiber

Kriegel, 2020-05-26:
Hallo!

Ersmal Danke SEHR für dieses Open Board!

Ich werde Facebook auch nicht nutzen und wage es meine Frage nun hier zu stellen.
Ich bin auch totaler newbee in sachen Elektronik und CNC.

Die Trinamic Treiber TMC2100, TMC2130 und TMC2208 werden in der GRBL Szene als Goldstandard bezeichnet.
Da diese die Stepper sehr leise betreiben sollen.

Siehe hier ein der übersicht über GRBL Schrittmotortreiber:
[https://www.filamentpreis.de/alles-ueber-schrittmotor-treiber/](https://www.filamentpreis.de/alles-ueber-schrittmotor-treiber/)

Laut Trinamic haben die Chips eine "Stallguard" Technologie.

Was ist Stallguard??
Video:
[https://www.youtube.com/watch?v=Prw7wNa20Gk](https://www.youtube.com/watch?v=Prw7wNa20Gk)
Infos:
[https://www.trinamic.com/technology/adv-technologies/](https://www.trinamic.com/technology/adv-technologies/)

Die Stallguard Technologie soll ähnlich wie Closed Loop funktionieren UND soll die Endschalter unnötig machen UND die Referenzfahrt ermöglichen.
Das ergibt auch Kostenersparnis....

Vergleich von Trinamic Chips und features siehe hier:
[https://learn.watterott.com/silentstepstick/comparison/](https://learn.watterott.com/silentstepstick/comparison/)

Nun meine Frage(n):
Könnte das Board die Trinamic Chips nutzen?
 z.B. auch den TMC2280 ohne Stallguard

Könnte das Board oder Estlcam Stallguard unterstützen?

Danke im Vorraus

Trinamic ist  eine deutsche Firma, wie geil ....

duke2421, 2020-05-26:
Moin, jain. Die Trinamics werden per SPI oder UART angesteuert, Auf diesem Board laufen werden sie, aber ohne die SPI/UART Verbindung zwischen µC und Treiber. Außerdem sind die im Stealth Chop Betrieb zwar leise haben aber weniger Kraft. Daher würde ich diese für meine Fräse eher nicht verwenden, da ist der Fräsmotor doch wesentlich lauter ;)
Am 3D-Drucker sind sie aber top.

tnn85, 2020-05-26:
Hallo @Kriegel

erstmal danke für die Blumen ;)
Ich war am Anfang der Entwicklung der Platine auch noch recht unerfahren was das Thema angeht und welche Treiber es gibt.
Soweit mir bekannt gibt es 3 verschiedene "Wege" die Schrittmotortreiber von der Steuerung anzusprechen:
1) Standalone (DIR/STEP-Signale)
2) UART (eine serielle Schnittstelle, die auch die Grundlage von der seriellen Schnittstelle bei PCs ist und auch einen Rückkanal und Parametrierung (z.b. Mikrosteps) zulässt)
3) SPI (eine andere serielle Schnittstelle, die oft auf Platinen zu finden ist mit den gleichen Vorteilen wie UART

Ich hab mich trotz der Fokussierung der Community auf die DRV8825-Treiber auch mit anderen Treibern beschäftigt und bin auch schnell auf die Trinamic-Treiber gestoßen, die mit ihren zahlreichen Funktionen tatsächlich sehr verlockend wirken.

Da die eigentlich Firmware von Estlcam  aber (zumindest aktuell) "Closed Source" ist, also ich daran nichts ändern konnte/kann, kann hätte ich ohne zusätzliche Mikrocontroller auf der Platine diese Funktion des "StallGuard" gar nicht unterstützen können.

Im Übrigen bietet der Treiber TMC2208 diese Funktion gar nicht an, sondern der TMC2209.

Klar wäre "sensorless Homing" eine tolle Funktion. Diese macht aber bei einem 3D-Drucker noch mehr sinn, als bei einer CNC-Fräse, bei der es auch ein bisschen ruppiger zugeht und es somit schwer wäre eine Endposition von einem ins Material eintauchen/einfräsen zu unterscheiden, bei dem der Widerstand auch höher als bei dem normalen Vorschub sein kann.

Beim CNC-Fräsen ist meist die absolute Position auch gar nicht so entscheidend, sondern eher das Werkstückkoordinantensystem.

Kriegel, 2020-05-29:
Ja,  "sensorless Homing" z.B  im Eilgang währe auch Kontraproduktiv ... *LOL*

Danke euch Sehr für die erhellenden Ausführungen und eure Zeit.

Bleibt gesund!

Closed 2020-05-29.

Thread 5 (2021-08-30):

GRBL support

derappelt, 2021-08-30:
In der Readme steht:
 (GRBL oder andere Firmware kann nach entsprechender Konfiguration auch mit der Platine verwendet werden)

Gibt es dazu mehr Details, wie eine entsprechende Konfiguration aussieht?

duke2421, 2021-08-30:
Wenn Du Estlcam schon hast, kannst Du Dir mein Video ansehen um GRBL auf dieses Board zu bekommen: https://www.youtube.com/watch?v=5jDialYKdVM

Ansonsten https://github.com/duke2421/grbl

derappelt, 2021-08-31:
Perfekt vielen Dank!

Closed 2021-08-31.

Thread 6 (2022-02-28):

Link zum bestellen des Bausatz-Set nicht mehr aktuell

notecp, 2022-02-28:
Hallo,

leider ist das Formular zur Bestellung des Sets nicht mehr aktiv :(
Gibt es einen neuen Link oder sonst eine Möglichkeit an ein Set zu kommen?

notecp, 2022-03-01:
Hallo Henrik,

super, dann wäre das geklärt. Ich stelle gerade die Kosten und Teile zusammen.
Gehe ich recht in der Annahme, dass bei dem Preis die DRV-Treiber und Arduino mit dabei ist?

Viele Grüße
Christian

Skudderon, 2022-03-01:
Ja, so ist es.

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

Skudderon, 2022-04-07:
Hallo Raini,

ganz einfach unter ***@***.*** ;)

Der Ablauf ist einfach:

1. ich brauch deine vollständige Postanschrift
2. Ein Set aus Platine, allen aufzulötenden Bauteile, allen nötigen Steckmodulen und Versand in Deutschland sind 60€ (andere Länder 5€ mehr)
3. schick die bitte mittels Paypal an Freunde an ***@***.*** oder alternativ als normale Zahlung (dann zuzüglich der 2€ Gebühr für Paypal).

Wenn das erledigt ist mach ich dein Paket fertig und schick es dir zu.

Viele Grüße
Henrik

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

lernsting, 2022-12-20:
Hallo Henrik,
Ich versuche dich mal hier zu erreichen.
Ich würde mir gerne eine MPCNC bauen und suche dafür noch das Tillboard. Hast du zufällig noch ein Bausatz parat?

Mfg Lars

Skudderon, 2022-12-20:
Hallo Lars,

ich versuche das möglichst unkompliziert zu machen:

1. Ich brauch deine vollständige Postanschrift
2. Ein Set aus Platine, allen aufzulötenden Bauteilen, dem DC-Konverter und Versand in Deutschland sind 55€ (andere Länder 5€ mehr)
3. schick die bitte mittels Paypal an Freunde an ***@***.*** oder alternativ als normale Zahlung (dann zuzüglich der 2€ Gebühr für Paypal).
Wenn das erledigt ist mach ich dein Paket fertig und schick es dir zu.

Wenn du eine Fräse mit externen Treibern baust brauchst du für die Steuerung lediglich noch einen Arduino Nano (z.B. von Amazon).
Für eine MPCNC kannst du 3 Treiber DRV8825 verwenden.

Viele Grüße
Henrik

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

lernsting, 2022-12-20:
Okay top. Danke für die schnelle Antwort!
Leider kann ich deine Mail Adresse nicht entziffern.

Gruß Lars

Skudderon, 2022-12-20:
Was meinst du damit du kannst ***@***.*** nicht entziffern?

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

lernsting, 2022-12-20:
Oder ist das mit den Sternchen richtig? 😅
Also ***@***.***

Skudderon, 2022-12-20:
Jetzt schick ich dir meine Mail mal als Bild.
Ich vermute du hast einen Filter in deinem Email-Programm laufen.

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

Skudderon, 2022-12-20:
Da deine Adresse jetzt auch aus lauter Sternchen bestand würde ich sagen GitHub verhindert die direkte Kommunikation

h . w o r g AT i c l o u d . c o m

schreib mir da mal

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

Doctor-BuZZ, 2022-12-24:
Hallo Henrik,

Bin auch gerade hier drüber gestolpert.
Kurze Frage wäre noch ein Bausatz verfügbar ?
Besten Dank für deine Rückmeldung.

Grüsse Christian

Skudderon, 2022-12-25:
Hallo Christian,ich hab noch eine Hand voll Bausätze.Github verhindert leider Details zu schreiben.Meld dich bitte mal unter:h . w o r g AT i c l o u d . c o mViele Grüße Henrik Von meinem iPhone gesendetAm 24.12.2022 um 09:41 schrieb Doctor-BuZZ ***@***.***>:
Hallo Henrik,
Bin auch gerade hier drüber gestolpert.
Kurze Frage wäre noch ein Bausatz verfügbar ?
Besten Dank für deine Rückmeldung.
Grüsse Christian

—Reply to this email directly, view it on GitHub, or unsubscribe.You are receiving this because you commented.Message ID: ***@***.***>

thomas-mitterer, 2023-03-19:
Hallo Henrik,

ich wollte dir eine Mail schreiben (an h.org@icloud.com), aber da kommt immer zurück.
Habe ich da vielleicht  die falsche?
Ich würde bitte ein Tillboard für die Volksfräse benötigen, kannst du mir da vielleicht weiterhelfen?

Gruß
Tom

Skudderon, 2023-03-19:
Hallo Thomas, das liegt vielleicht daran daß ich Worg heiße und nicht Org. 🤣🤣Mit ***@***.*** sollte es funktionieren. 😉Ich versuche das möglichst unkompliziert zu machen:1. Ich brauch deine vollständige Postanschrift2. Ein Set aus Platine, allen aufzulötenden Bauteilen, dem DC-Konverter und Versand in Deutschland sind 55€ (andere Länder 5€ mehr)3. schick die bitte mittels Paypal an Freunde an ***@***.*** oder alternativ als normale Zahlung (dann zuzüglich der 2€ Gebühr für Paypal).Wenn das erledigt ist mach ich dein Paket fertig und schick es dir zu.Wenn du eine Fräse mit externen Treibern baust brauchst du für die Steuerung lediglich noch einen Arduino Nano (z.B. von Amazon). Für eine MPCNC kannst du 3 Treiber DRV8825 verwenden.Viele GrüßeHenrikAm 19.03.2023 um 13:12 schrieb thomas-mitterer ***@***.***>:
Hallo Henrik,
ich wollte dir eine Mail schreiben (an ***@***.***), aber da kommt immer zurück.
Habe ich da vielleicht  die falsche?
Ich würde bitte ein Tillboard für die Volksfräse benötigen, kannst du mir da vielleicht weiterhelfen?
Gruß
Tom

—Reply to this email directly, view it on GitHub, or unsubscribe.You are receiving this because you commented.Message ID: ***@***.***>

thomas-mitterer, 2023-03-19:
Vielen Dank. Alles klar, Userfehler.🤦‍♂️
Ich kann leider die Adresse für die Zahlung nicht lesen. Da sehe ich nur Punkte.

Gruß Thomas

Skudderon, 2023-03-19:
Dann hast du über Github geschrieben. Das filtert alle Mailadressen raus.Aber ich hab gesehen daß deine Zahlung angekommen ist.Adresse hab ich gesehen.Dein Set geht gleich morgen zu DHL.Viele Grüße Am 19.03.2023 um 16:48 schrieb thomas-mitterer ***@***.***>:
Vielen Dank. Alles klar, Userfehler.🤦‍♂️
Ich kann leider die Adresse für die Zahlung nicht lesen. Da sehe ich nur Punkte.
Gruß Thomas

—Reply to this email directly, view it on GitHub, or unsubscribe.You are receiving this because you commented.Message ID: ***@***.***>

LowRob1, 2023-06-01:
Hallo Henrik. Gibt es noch irgendwo fertige Boards zu kaufen oder nur noch Bausätze?

Gruß Robert

Ku3tti, 2024-03-09:
Grüß dich, sag mal hast du noch zwei Bausätze übrig?

Maja283, 2024-12-28:
Hallo Hendrik, ich würde auch gerne einen Bausatz noch nehmen, falls noch welche übrig seien sollten.
Liebe Grüße
Maja

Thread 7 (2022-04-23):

Bestellung des Shields

Holzhacker71, 2022-04-23:
Hallo ich wollte mal nachfragen ob noch Bausätze giebt?
Und ob mann die Platiene auch fertig bestückt erwerbenkann?

tnn85, 2022-07-20:
Hallo, verspätete Antwort aber für andere möglicherweise interessant:
Ich habe keine Bausätze mehr und vertreibe die selbst auch schon lange nicht mehr.
Es gab zwischen mir und @Skudderon eine Vereinbarung, dass er die Dinger vertreibt. Möglich, dass er noch Restbestände hat.
Ich bin raus.

Closed 2022-07-20.

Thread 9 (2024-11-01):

Arduino mit Estelcam

Janilp19, 2024-11-01:
Ich habe den Arduino mit estelcam so verbunden wie es beim Onkel auch ist aber es ging nicht. Dann habe ich es ohne Bord probiert und es ging. Ich habe nochmal alle Lötstellen kontrolliert und kann den Fehler nicht finden
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

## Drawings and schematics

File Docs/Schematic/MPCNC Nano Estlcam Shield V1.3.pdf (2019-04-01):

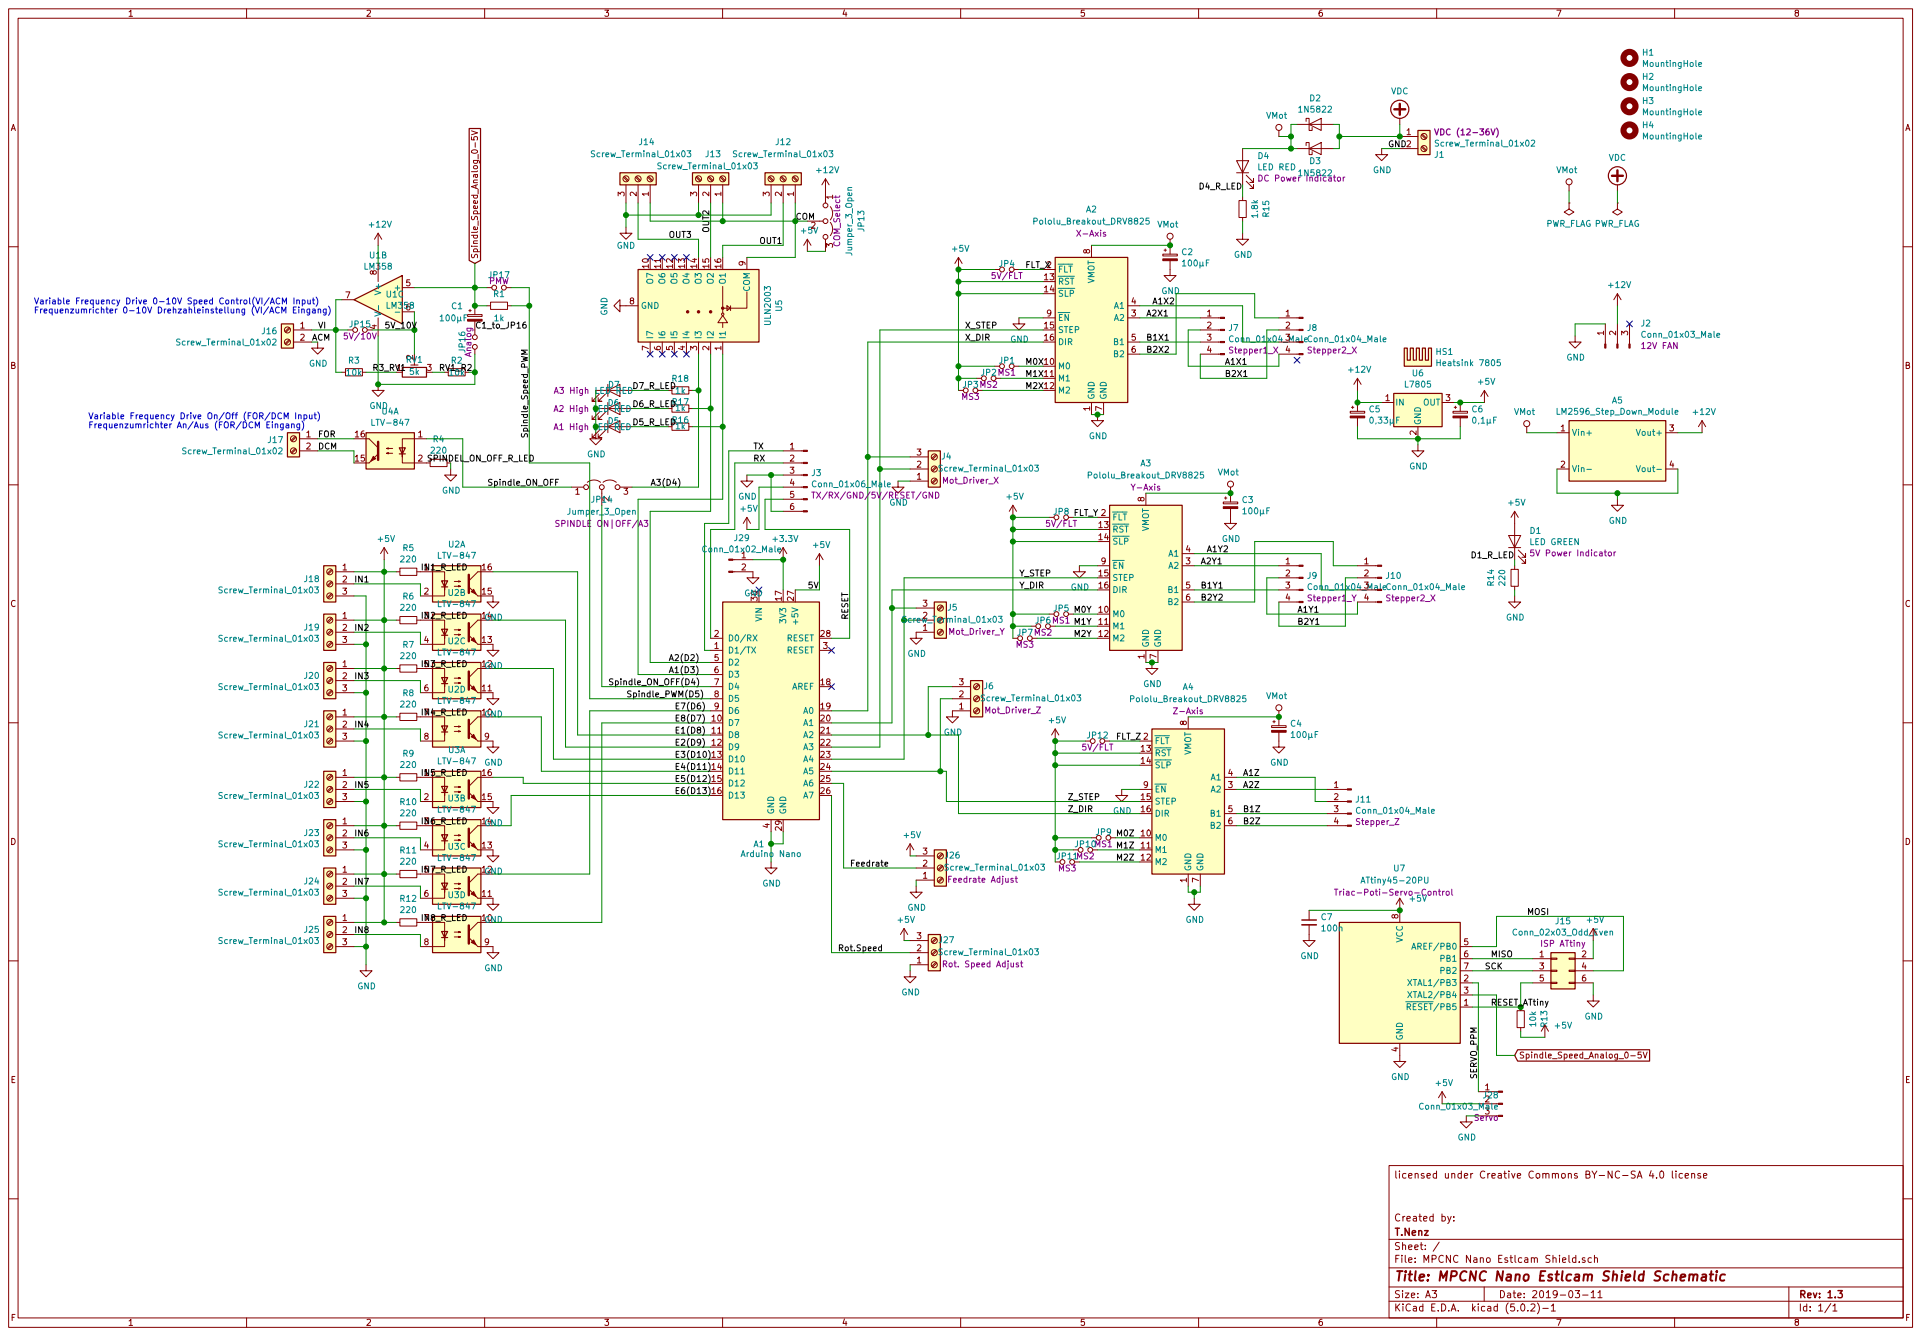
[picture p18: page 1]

8 EN 9 A2 Pololu_Breakout_DRV8825 X-Axis GND GND

1 M0 10 M1 11 M2 12 RST 13 SLP 14 STEP 15 DIR 16 FLT 2 A2 3 A1 4 B1 5 B2 6 GND

Variable Frequency Drive 0-10V Speed Control(VI/ACM Input)

X_DIR

D7 A3 High LED RED GND
1k D6 A2 High LED RED
D5 A1 High LED RED

J17 Screw_Terminal_01x02 Variable Frequency Drive On/Off (FOR/DCM Input)
Frequenzumrichter An/Aus (FOR/DCM Eingang)

2 IN3 | 11

8 EN 9 A4 Pololu_Breakout_DRV8825 Z-Axis GND GND

2 IN4

5V/FLT
Triac-Poti-Servo-Control +5V GND

E4(D11)
E5(D12)

Z_DIR

licensed under Creative Commons BY-NC-SA 4.0 license

File: MPCNC Nano Estlcam Shield.sch Sheet: / T.Nenz Created by:

Id: 1/1 Title: MPCNC Nano Estlcam Shield Schematic

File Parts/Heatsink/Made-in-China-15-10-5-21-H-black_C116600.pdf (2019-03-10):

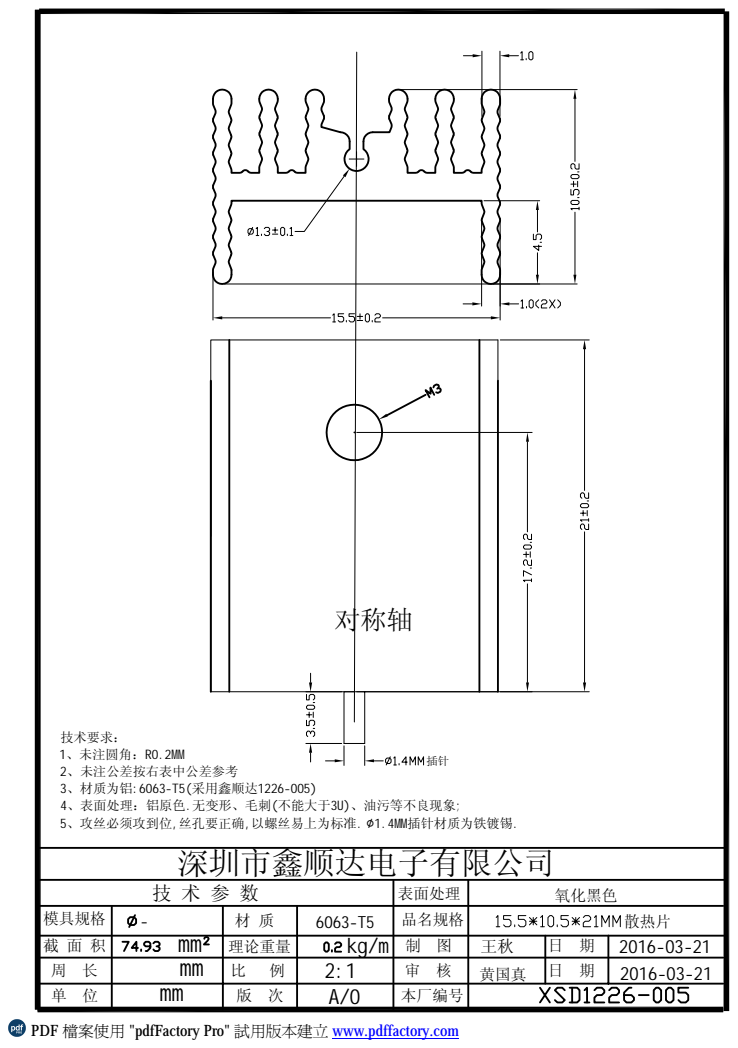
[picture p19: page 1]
理论重量; 品名规格; 本厂编号; 深圳市鑫顺达电子有限公司; 模具规格; 氧化黑色; 表面处理; 对称轴; 散热片; 黄国真

技术要求：
1、未注圆角：R0.2MM
2、未注公差按右表中公差参考
3、材质为铝:6063-T5(采用鑫顺达1226-005)
4、表面处理：铝原色.无变形、毛刺(不能大于3U)、油污等不良现象;
5、攻丝必须攻到位,丝孔要正确,以螺丝易上为标准. ∅1.4MM插针材质为铁镀锡.

PDF 檔案使用 "pdfFactory Pro" 試用版本建立 www.pdffactory.com

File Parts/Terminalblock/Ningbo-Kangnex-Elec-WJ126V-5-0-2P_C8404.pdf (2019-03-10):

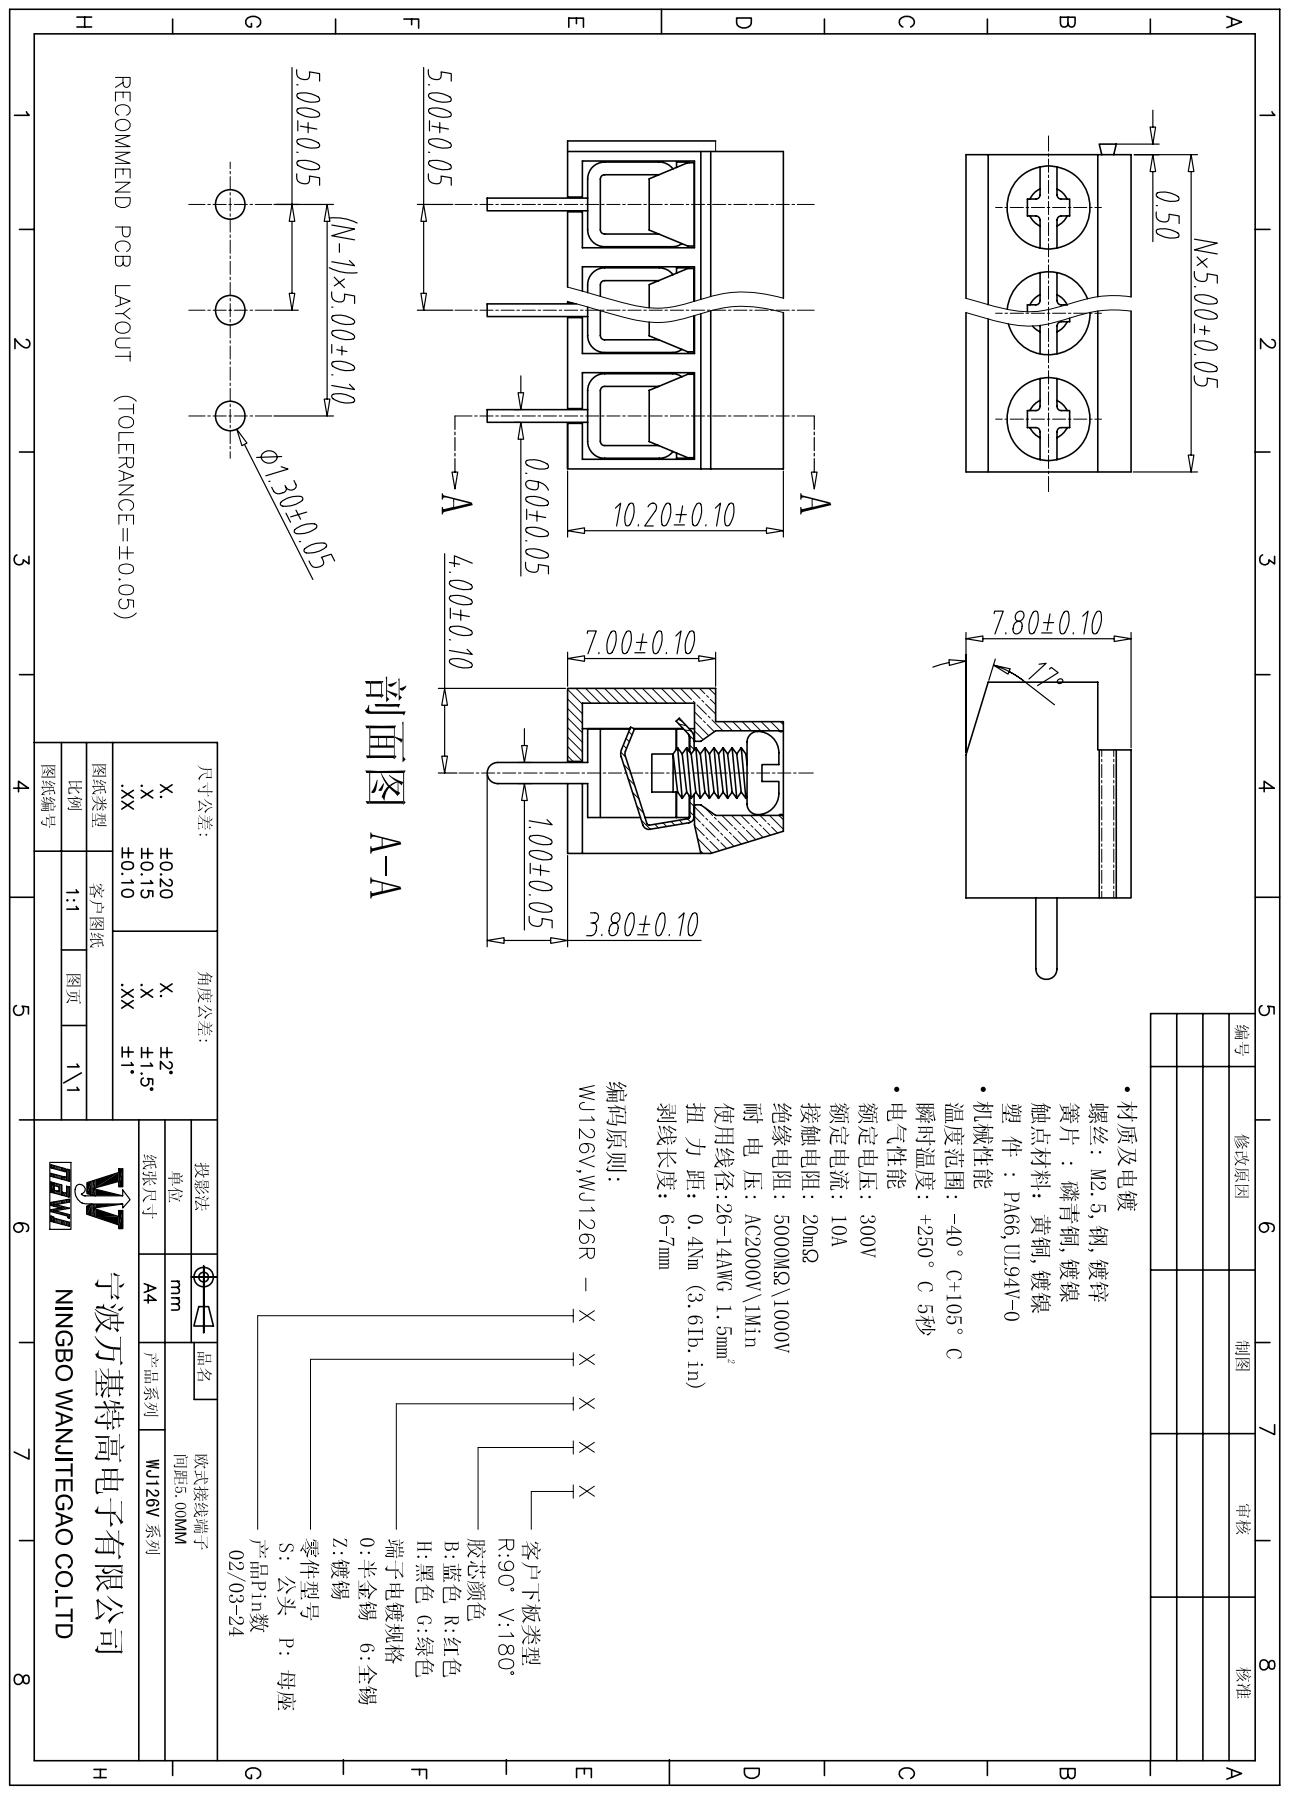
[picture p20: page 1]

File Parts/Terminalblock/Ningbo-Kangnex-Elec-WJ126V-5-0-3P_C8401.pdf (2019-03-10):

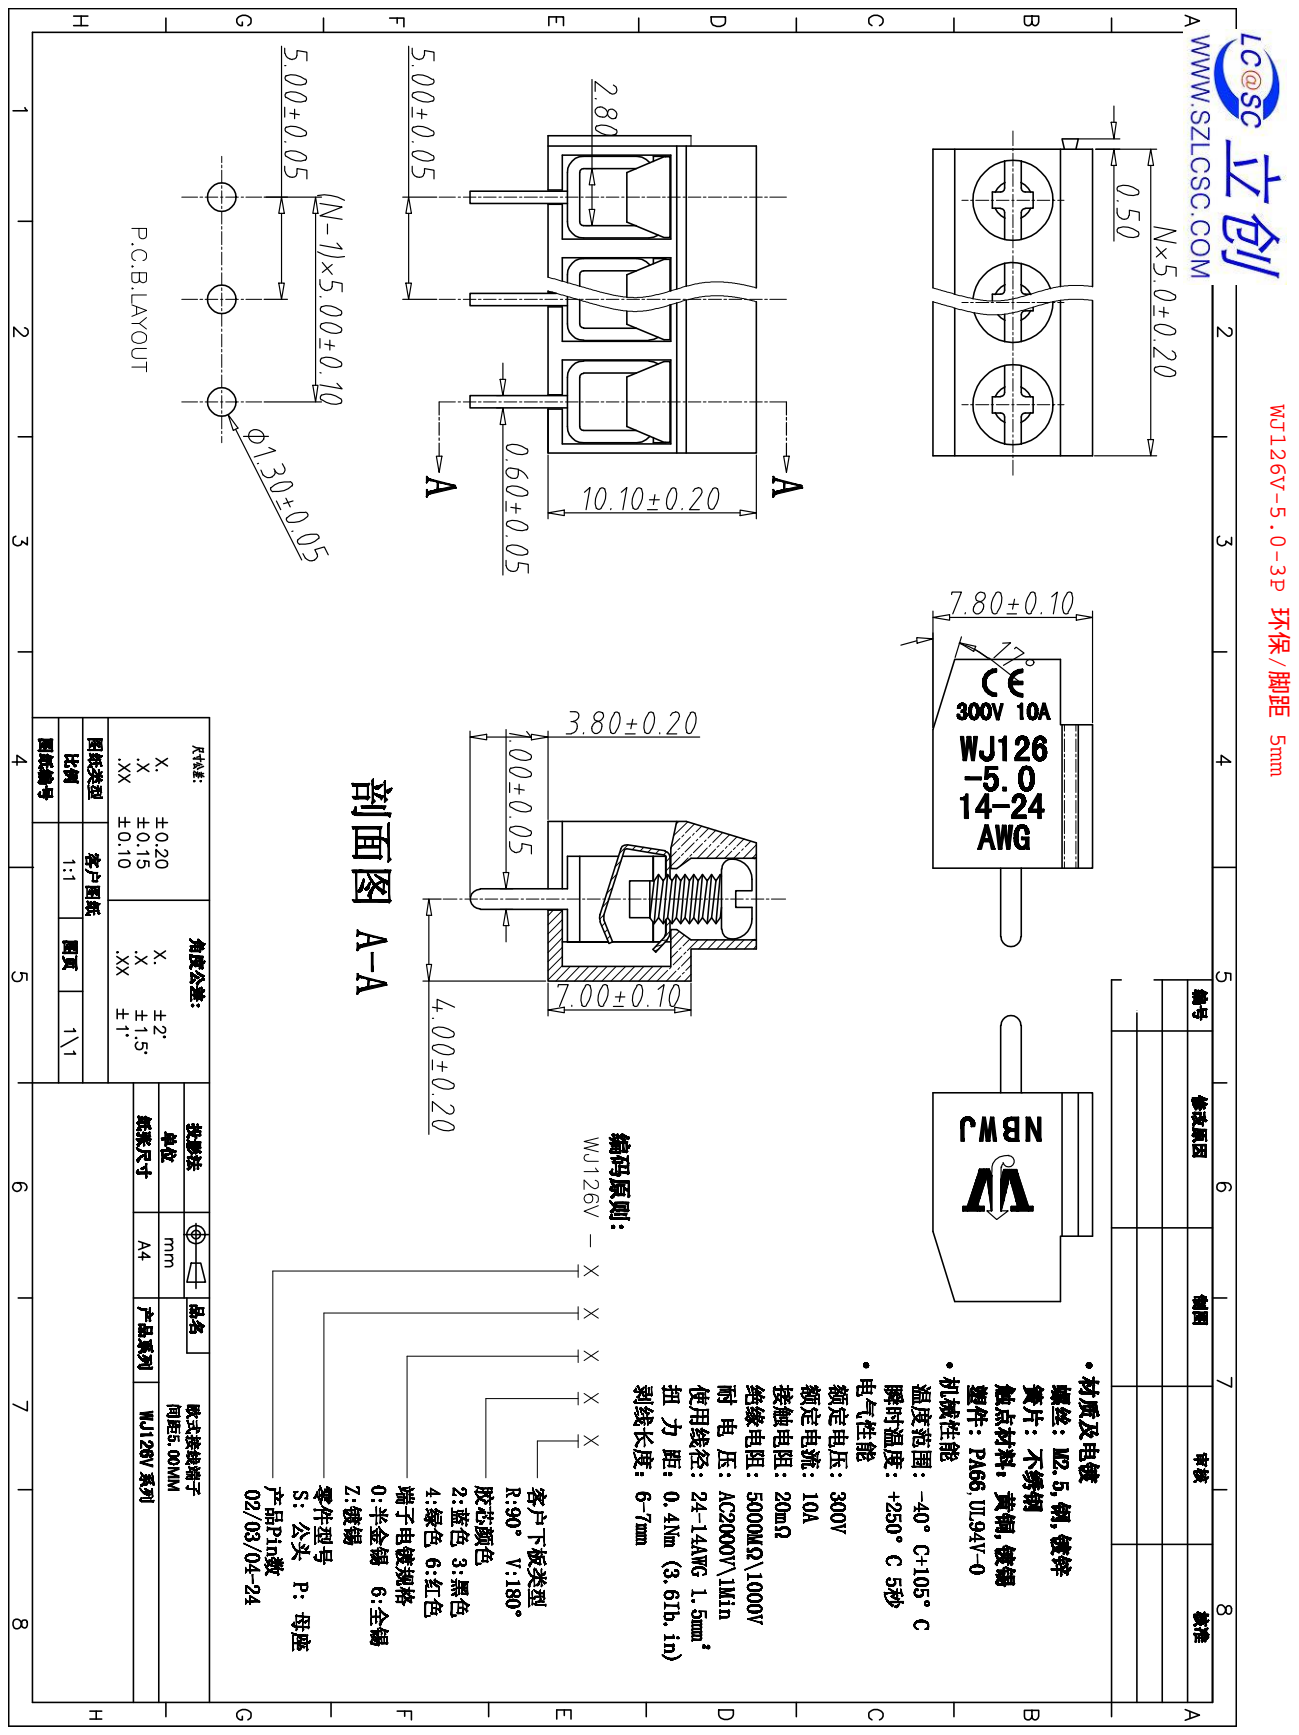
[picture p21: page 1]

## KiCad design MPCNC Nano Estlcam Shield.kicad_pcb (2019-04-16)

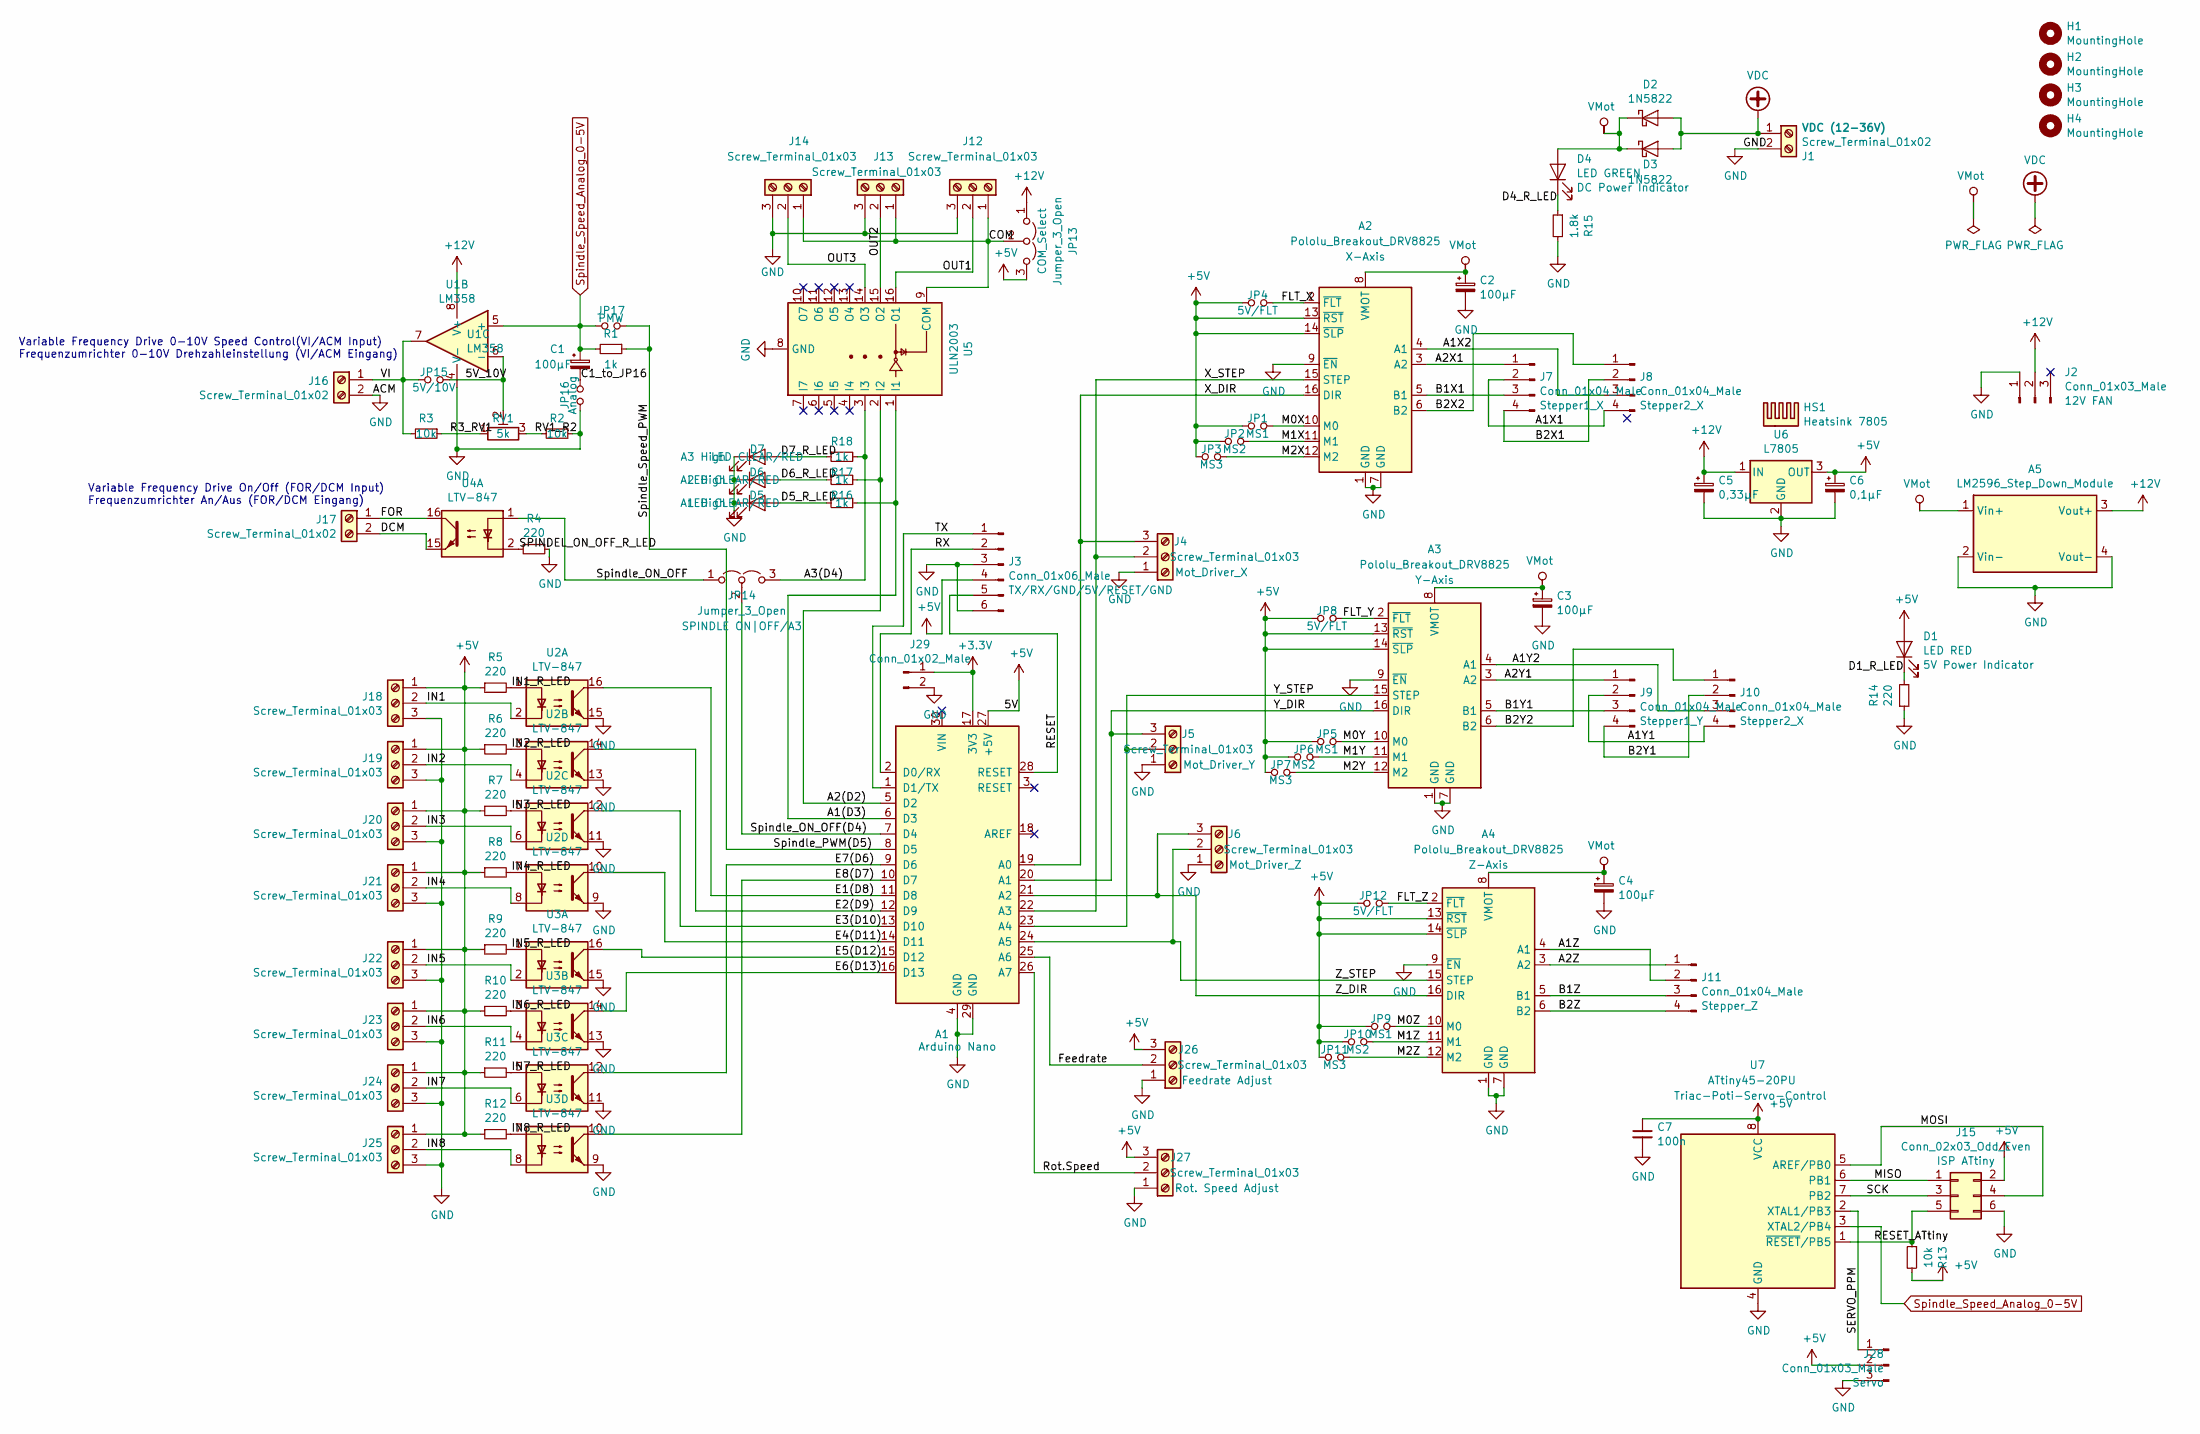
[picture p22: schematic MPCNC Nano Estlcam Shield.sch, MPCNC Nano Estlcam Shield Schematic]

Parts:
A1: Arduino Nano; Arduino_Nano
A2, A3, A4: Pololu_Breakout_DRV8825; Pololu_Breakout-16_15.2x20.3mm
A5: LM2596_Step_Down_Module; LM2596_Step_Down_Module-21.3x43.6mm
C1, C2, C3, C4: 100µF; CP_Radial_D8.0mm_P3.50mm
C5: 0,33µF; CP_Radial_D5.0mm_P2.00mm
C6: 0,1µF; CP_Radial_D5.0mm_P2.00mm
C7: 100n; C_Disc_D3.0mm_W1.6mm_P2.50mm
D1: LED RED; LED_D5.0mm_Red
D2, D3: 1N5822; D_DO-201AD_P15.24mm_Horizontal
D4: LED GREEN; LED_D5.0mm_Green
D5, D6, D7: LED CLEAR/RED; LED_D3.0mm_Clear
H1, H2, H3, H4: MountingHole; MountingHole_4.3mm_M4_DIN965_Pad
HS1: Heatsink 7805; Heatsink_China_TO220_(22x)15x10mm_1xDrill1.5mm
J1, J16, J17: Screw_Terminal_01x02; TerminalBlock_RND_205-00012_1x02_P5.00mm_Horizontal
J2: Conn_01x03_Male; Molex_KK-254_AE-6410-03A_1x03_P2.54mm_Vertical
J3: Conn_01x06_Male; PinHeader_1x06_P2.54mm_Vertical
J4, J5, J6, J12, J13, J14, J18, J19, J20, J21, J22, J23, J24, J25, J26, J27: Screw_Terminal_01x03; TerminalBlock_RND_205-00013_1x03_P5.00mm_Horizontal
J7, J8, J9, J10, J11: Conn_01x04_Male; PinHeader_1x04_P2.54mm_Vertical
J15: Conn_02x03_Odd_Even; PinHeader_2x03_P2.54mm_Vertical
J28: Conn_01x03_Male; PinHeader_1x03_P2.54mm_Vertical
J29: Conn_01x02_Male; PinHeader_1x02_P2.54mm_Vertical
JP1, JP2, JP3, JP4, JP5, JP6, JP7, JP8, JP9, JP10, JP11, JP12, JP15, JP16, JP17: Jumper_NO_Small; PinHeader_1x02_P2.54mm_Vertical
JP13, JP14: Jumper_3_Open; PinHeader_1x03_P2.54mm_Vertical
R1, R16, R17, R18: 1k; R_Axial_DIN0207_L6.3mm_D2.5mm_P7.62mm_Horizontal
R2, R3, R13: 10k; R_Axial_DIN0207_L6.3mm_D2.5mm_P7.62mm_Horizontal
R4, R5, R6, R7, R8, R9, R10, R11, R12, R14: 220; R_Axial_DIN0207_L6.3mm_D2.5mm_P7.62mm_Horizontal
R15: 1.8k; R_Axial_DIN0207_L6.3mm_D2.5mm_P7.62mm_Horizontal
RV1: 5k; Potentiometer_Bourns_3296W_Vertical
U1: LM358; DIP-8_W7.62mm
U2, U3, U4: LTV-847; DIP-16_W7.62mm
U5: ULN2003; DIP-16_W7.62mm
U6: L7805; TO-220-3_Vertical
U7: ATtiny45-20PU; DIP-8_W7.62mm

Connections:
+3V3: A1.17 (3V3), J29.1
+5V: A1.27 (+5V), A2.13 (~RST), A2.14 (~SLP), A3.13 (~RST), A3.14 (~SLP), A4.13 (~RST), A4.14 (~SLP), C6.1, C7.1, D1.2 (A), J3.4, J15.2, J18.1, J19.1, J20.1, J21.1, J22.1, J23.1, J24.1, J25.1, J26.3, J27.3, J28.2, JP1.1, JP2.1, JP3.1, JP4.1, JP5.1, JP6.1, JP7.1, JP8.1, JP9.1, JP10.1, JP11.1, JP12.1, JP13.3 (B), R5.1, R6.1, R7.1, R8.1, R9.1, R10.1, R11.1, R12.1, R13.2, U6.3 (OUT), U7.8 (VCC)
+12V: A5.3 (Vout+), C5.1, J2.2, JP13.1 (A), U1.8 (V+), U6.1 (IN)
/5V_10V: JP15.2, RV1.2, U1.6 (-)
/A1(D3): A1.6 (D3), R16.1, U5.1 (I1)
/A1X1: J7.2, J8.4
/A1X2: A2.4 (A1), J8.3
/A1Y1: J9.2, J10.4
/A1Y2: A3.4 (A1), J10.3
/A1Z: A4.4 (A1), J11.2
/A2(D2): A1.5 (D2), R17.1, U5.2 (I2)
/A2X1: A2.3 (A2), J7.1
/A2Y1: A3.3 (A2), J9.1
/A2Z: A4.3 (A2), J11.1
/A3(D4): JP14.3 (B), R18.2, U5.3 (I3)
/B1X1: A2.5 (B1), J7.3
/B1Y1: A3.5 (B1), J9.3
/B1Z: A4.5 (B1), J11.3
/B2X1: J7.4, J8.2
/B2X2: A2.6 (B2), J8.1
/B2Y1: J9.4, J10.2
/B2Y2: A3.6 (B2), J10.1
/B2Z: A4.6 (B2), J11.4
/C1_to_JP16: C1.2, JP16.1
/COM: J12.1, J13.1, J14.1, JP13.2 (C), U5.9 (COM)
/D1_R_LED: D1.1 (K), R14.2
/D4_R_LED: D4.1 (K), R15.1
/D5_R_LED: D5.2 (A), R16.2
/D6_R_LED: D6.2 (A), R17.2
/D7_R_LED: D7.2 (A), R18.1
/DCM: J17.2, U4.15
/E1(D8): A1.11 (D8), U2.16
/E2(D9): A1.12 (D9), U2.14
/E3(D10): A1.13 (D10), U2.12
/E4(D11): A1.14 (D11), U2.10
/E5(D12): A1.15 (D12), U3.16
/E6(D13): A1.16 (D13), U3.14
/E7(D6): A1.9 (D6), U3.12
/E8(D7): A1.10 (D7), U3.10
/FLT_X: A2.2 (~FLT), JP4.2
/FLT_Y: A3.2 (~FLT), JP8.2
/FLT_Z: A4.2 (~FLT), JP12.2
/FOR: J17.1, U4.16
/Feedrate: A1.25 (A6), J26.2
/IN1: J18.2, U2.2
/IN1_R_LED: R5.2, U2.1
/IN2: J19.2, U2.4
/IN2_R_LED: R6.2, U2.3
/IN3: J20.2, U2.6
/IN3_R_LED: R7.2, U2.5
/IN4: J21.2, U2.8
/IN4_R_LED: R8.2, U2.7
/IN5: J22.2, U3.2
/IN5_R_LED: R9.2, U3.1
/IN6: J23.2, U3.4
/IN6_R_LED: R10.2, U3.3
/IN7: J24.2, U3.6
/IN7_R_LED: R11.2, U3.5
/IN8: J25.2, U3.8
/IN8_R_LED: R12.2, U3.7
/M0X: A2.10 (M0), JP1.2
/M0Y: A3.10 (M0), JP5.2
/M0Z: A4.10 (M0), JP9.2
/M1X: A2.11 (M1), JP2.2
/M1Y: A3.11 (M1), JP6.2
/M1Z: A4.11 (M1), JP10.2
/M2X: A2.12 (M2), JP3.2
/M2Y: A3.12 (M2), JP7.2
/M2Z: A4.12 (M2), JP11.2
/MISO: J15.1, U7.6 (PB1)
/MOSI: J15.4, U7.5 (AREF/PB0)
/OUT1: J12.2, U5.16 (O1)
/OUT2: J13.2, U5.15 (O2)
/OUT3: J14.2, U5.14 (O3)
/R3_RV1: R3.1, RV1.1
/RESET: A1.28 (RESET), J3.5
/RESET_ATtiny: J15.5, R13.1, U7.1 (~RESET~/PB5)
/RV1_R2: R2.2, RV1.3
/RX: A1.2 (D0/RX), J3.2
/Rot.Speed: A1.26 (A7), J27.2
/SCK: J15.3, U7.7 (PB2)
/SERVO_PPM: J28.1, U7.2 (XTAL1/PB3)
/SPINDEL_ON_OFF_R_LED: R4.2, U4.2
/Spindle_ON_OFF: JP14.1 (A), U4.1
/Spindle_ON_OFF(D4): A1.7 (D4), JP14.2 (C)
/Spindle_PWM(D5): A1.8 (D5), JP17.1, R1.1
/TX: A1.1 (D1/TX), J3.1
/VI: J16.1, JP15.1, R3.2, U1.7
/X_DIR: A1.19 (A0), A2.16 (DIR), J4.3
/X_STEP: A1.22 (A3), A2.15 (STEP), J4.2
/Y_DIR: A1.20 (A1), A3.16 (DIR), J5.3
/Y_STEP: A1.23 (A4), A3.15 (STEP), J5.2
/Z_DIR: A1.21 (A2), A4.16 (DIR), J6.3
/Z_STEP: A1.24 (A5), A4.15 (STEP), J6.2
GND: A1.4 (GND), A1.29 (GND), A2.1 (GND), A2.7 (GND), A2.9 (~EN), A3.1 (GND), A3.7 (GND), A3.9 (~EN), A4.1 (GND), A4.7 (GND), A4.9 (~EN), A5.2 (Vin-), A5.4 (Vout-), C2.2, C3.2, C4.2, C5.2, C6.2, C7.2, D5.1 (K), D6.1 (K), D7.1 (K), J1.2, J2.1, J3.3, J3.6, J4.1, J5.1, J6.1, J12.3, J13.3, J14.3, J15.6, J16.2, J18.3, J19.3, J20.3, J21.3, J22.3, J23.3, J24.3, J25.3, J26.1, J27.1, J28.3, J29.2, JP16.2, R2.1, R4.1, R14.1, R15.2, U1.4 (V-), U2.9, U2.11, U2.13, U2.15, U3.9, U3.11, U3.13, U3.15, U5.8 (GND), U6.2 (GND), U7.4 (GND)
Spindle_Speed_Analog_0-5V: C1.1, JP17.2, R1.2, U1.5 (+), U7.3 (XTAL2/PB4)
VDC: D2.2 (A), D3.2 (A), J1.1
VMot: A2.8 (VMOT), A3.8 (VMOT), A4.8 (VMOT), A5.1 (Vin+), C2.1, C3.1, C4.1, D2.1 (K), D3.1 (K), D4.2 (A)

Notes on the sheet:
Variable Frequency Drive On/Off (FOR/DCM Input) Frequenzumrichter An/Aus (FOR/DCM Eingang)
Variable Frequency Drive 0-10V Speed Control(VI/ACM Input) Frequenzumrichter 0-10V Drehzahleinstellung (VI/ACM Eingang)

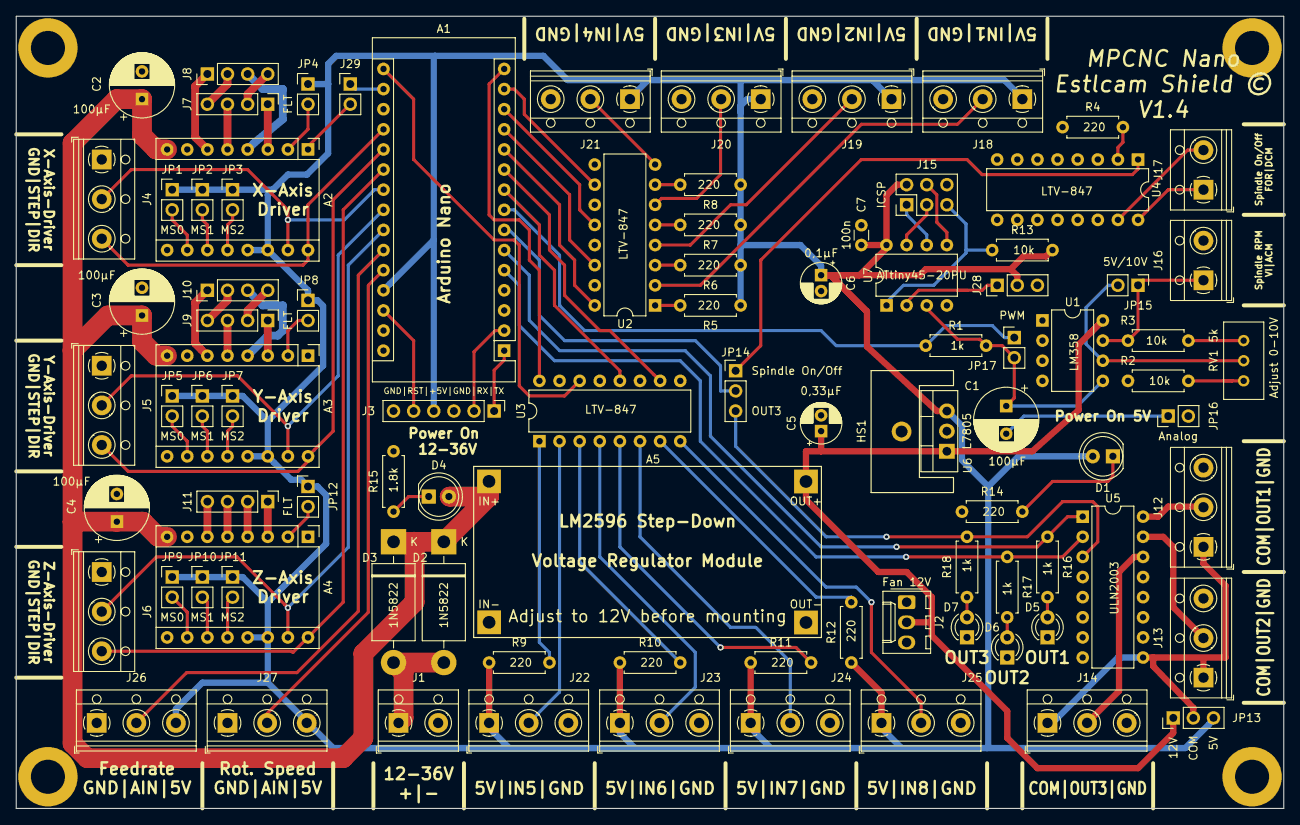
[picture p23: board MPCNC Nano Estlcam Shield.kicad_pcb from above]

Board: 2 copper layers, 160.0 x 100.0 mm, 96 parts (0 on the bottom side), 98 nets.

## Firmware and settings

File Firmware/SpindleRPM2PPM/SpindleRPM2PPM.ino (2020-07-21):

/*
 * Spindle RPM-Signal to PPM-Signal conversion (e.g. for controlling RC model motor with ESCs, RC model servos)  
 * 
 * Author: Till Nenz
 * Date: 20.07.2020
 * Version: 0.1
 * 
 * Description:
 * Reads an analog input pin (Signal "Spindle_Speed_Analog_0-5V"), 
 * maps the result to a range from MIN_PPM_PULSE (default 1000µs) to MAX_PPM_PULSE (default 2000µs) and uses
 * the result to set the pulse pause modulated signal (PPM) of an output pin (Signal "Servo_PPM").
 * Debug: If activated, prints the results to the Serial Monitor (however, this causes the servo signal to jitter and should only be used to debug).
 * 
 * Required IC:
 * -ATtiny25/45/85-20PU (Package: PDIP) (tested with ATtiny85) (ATtiny 25 Program space might be too small for future releases)
 * 
 * Required Software:
 * -Arduino IDE 1.8.13 or newer
 * -ATTiny Core by SpenceKonde (https://github.com/SpenceKonde/ATTinyCore/blob/master/Installation.md)
 * 
 * Required chip fuse settings:
 * -ATtiny fuse bytes have to be programmed before flashing this firmware
 * -Low Fuse: 0xE2; High Fuse: 0xDF; Extended Fuse: 0xFF;  (AVRDUDE: -U lfuse:w:0xe2:m -U hfuse:w:0xdf:m -U efuse:w:0xff:m)
 * 
 * The circuit:
 *   - see "MPCNC Nano Estlcam Shield V1.x.pdf" schematic
 *   - connect Servo/ESC to J28 pin header (white cable [servo signal] left pin [facing to the µC/ATtiny], red cable [VCC/5V] middle pin, black cable [GND] right pin)
 *   - UART debug output (Baud: 115200 bit/s) on MOSI pin (Pin 5/PB0/Arduino Pin 0) (see https://github.com/SpenceKonde/ATTinyCore/blob/master/avr/extras/ATtiny_x5.md) connected to the ICSP header
 * 
 * based on:   
 * https://github.com/SpenceKonde/ATTinyCore/blob/master/avr/libraries/Servo_ATTinyCore/examples/Knob/Knob.ino
 * 
 */

#include <Servo_ATTinyCore.h>

//#define DEBUG_SERIAL

// Pin definitions
#define ANALOG_SPINDLE_RPM_IN_PIN  A2  // Analog input pin that the Arduino Nano spindle RPM signal is attached to
#define PPM_SPINDLE_RPM_OUT_PIN  3 //  // Digital output pin that the motor ESC / servo is attached to

// ESC/Servo PPM pulse length [µs]
#define MIN_PPM_PULSE 1000
#define MAX_PPM_PULSE 2000

int analogSpindleRPMValue = 0;        // value read from the input spindle RPM signal
int ppmSpindleRPMValue = 0;           // value pulse length [µ output to the PPM 

Servo servo_esc;  // create servo object to control an esc or servo

void setup() {
#ifdef DEBUG_SERIAL
  // initialize serial communications at 115200 bps:
  Serial.begin(115200);
  //ACSR &=~(1<<ACIE);  //Turn off UART Tx
  //ACSR |=~(1<<ACD);   //Turn off UART Tx
#endif
  servo_esc.attach(PPM_SPINDLE_RPM_OUT_PIN, MIN_PPM_PULSE, MAX_PPM_PULSE);  // attaches the servo on pin PPM_SPINDLE_RPM_OUT_PIN to the servo object and sets min and max values for writes (in µs). 

}

void loop() {
  // read the analog in value:
  analogSpindleRPMValue = analogRead(ANALOG_SPINDLE_RPM_IN_PIN);
  // map it to the range of the analog out:
  ppmSpindleRPMValue = map(analogSpindleRPMValue, 0, 1023, MIN_PPM_PULSE, MAX_PPM_PULSE);
    
  //servo_esc.writeMicroseconds( (int) ppmSpindleRPMValueAvg.getAverage());  // sets the servo position according to the scaled value
  servo_esc.writeMicroseconds(ppmSpindleRPMValue);  // sets the servo position according to the scaled value


  // wait 15 milliseconds before the next loop for the analog-to-digital
  // converter to settle after the last reading and the esc/servo to geht there:
  delay(15); // waits for the servo to get there

#ifdef DEBUG_SERIAL
  // print the results to the Serial Monitor:
  //Serial.print("Spindle RPM [0..1023]= "); // Spindle RPM measured on ADC [0..1023]
  //Serial.print(analogSpindleRPMValue);
  //Serial.print("\t Servo/ESC pulse length= "); // Servo/ESC output PPM signal pulse length [MIN_PPM_PULSE µs..MAX_PPM_PULSE µs] 
  //Serial.println(ppmSpindleRPMValue);
#endif

}

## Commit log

2019-02-28 First commit
    First commit to Version 1.0 to Repo
    [MPCNC Nano Estlcam Shield.kicad_pcb, MPCNC Nano Estlcam Shield.sch]
2019-03-04 V1.1
    - Version 1.1 of MPCNC Nano Estlcam Shield
    PCB schematic changes:
    # Symbol value removed (default symbol value for BOM creation)
    + Added field value "Funktion" to all symbols for part description
    # Symbol reference annotation changed
    + 12-36V power supply capability (with LM2596 Step Down Module)
    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
    [MPCNC Nano Estlcam Shield.kicad_pcb, MPCNC Nano Estlcam Shield.sch]
2019-03-10 V1.2
    - Version 1.2 of MPCNC Nano Estlcam Shield
    + Power LEDs (5mm LED) added(5V and VMot[formerly VDD])
    + 3,3V connector added
    + Output Enabled LEDs added (3 x 3mm LED + 1k resistor for OUT1,2,3), Pulls down ouput signal on startup
    # Replaced powerflag "VDD" with "VMot" (new custom symbol)
    + Added net names for Microstepping jumper
    # Signal "Analog_0_5V" now connected to "LM358 +"-Pin net (after instead of before LP-filter)
    # Replaced servo connector symbol (Conn_01x03_Female to Conn_01x03_Male)
    # Mirrored Microstepping and FLT jumper (Pin 1:5V, Pin 2:Signal)
    # Changed net names ("Ex"-> "INx", "Ax" -> "OUTx")
    PCB layout changes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
    [BOM MPCNC Nano Estlcam Shield.csv, Current Consumption Calculation.xlsx, LCSC_Exported_20190306_133505.xlsx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]
2019-03-10 Revert "V1.2"
    This reverts commit 25746ea092c74b1b8c6b498096b07c9fdffcdb93.
    [BOM MPCNC Nano Estlcam Shield.csv, Current Consumption Calculation.xlsx, LCSC_Exported_20190306_133505.xlsx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]
2019-03-10 Revert "Revert "V1.2""
    This reverts commit 57979cb871c24b21395862369d7dbde15bbed53b.
    [BOM MPCNC Nano Estlcam Shield.csv, Current Consumption Calculation.xlsx, LCSC_Exported_20190306_133505.xlsx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]
2019-03-12 V1.3
    - Version 1.3 of MPCNC Nano Estlcam Shield
    # Changed electrolytic capacitor values for L7805 (0,33µF + 0,1µF)
    PCB layout changes:
    # Changed footprint of electrolytic capacitor for L7805 (D=8mm/RM=3,5mm -> D=5mm/RM=2,0mm)
    # Revised heatsink footprint
    + Footprints for many components added to project footprint library ("MPCNC_Shield_Footprints"). Modified footprints from standard KiCad library with value on
    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
    [MPCNC Nano Estlcam Shield.kicad_pcb, MPCNC Nano Estlcam Shield.sch]
2019-03-12 Minor changes for V1.3
    #Changed footprints for some parts from standard lib to MPCNC lib
    #Added value to silk screen layer for some footprints
    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
    [MPCNC Nano Estlcam Shield.kicad_pcb, MPCNC Nano Estlcam Shield.sch]
2019-04-01 Public Release V1.3
    [BOM MPCNC Nano Estlcam Shield V1.3.csv, BOM MPCNC Nano Estlcam Shield.csv, Current Consumption Calculation.xlsx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]
2019-04-14 Delete Unterteil.step
    Wird durch eine andere Datei ersetzt
    [Unterteil.step]
2019-04-14 Changes
    Ein paar kleine Anpassungen
    [Frontplatte-Blanko.step, Frontplatte-Komplett.step, Oberteil-Blanko.step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]
2019-04-14 Delete Frontplatte-DSUB-Hohlbuchse.stl
    Ersatz durch neue Datei
    [Frontplatte-DSUB-Hohlbuchse.stl]
2019-04-14 Changes
    Ein paar kleinere Updates an der Datei.
    [Frontplatte-Blanko.stl, Frontplatte-komplett.stl, Oberteil-70mm-Luefter.stl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]
2019-04-14 Add files via upload
    DXF zum Fräsen der Frontplatte
    [Frontplatte.dxf]
2019-04-14 Moved to separate folder
    - separate folder for each enclosure contributor
    - minor changes in README.md
    [Frontplatte-Blanko.step, Frontplatte-Blanko.stl, Frontplatte-Komplett.step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]
2019-04-16 V1.4
    - Version 1.4 of MPCNC Nano Estlcam Shield
    # Changed LED colours (D1:red, D4:green, D5-7:Clear/red)
    + Footprints for LEDs added to project footprint library ("MPCNC_Shield_Footprints").
    # Changed footprint of LEDs
    # Moved silk screen reference fo L7805 (U6). Reference was hidden by heatsink
    + Added LED 3D models to footprint. LEDs show correct color for 3D model (green, red, white[clear])
    # Changed 3D model for potentiometer (KiCAD standard library model now available in latest KiCAD release 5.10)
    # Changed 3D model for screw terminal blocks (J1; J4-6; J12-14; J16-J17; J18-27)
    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
    [MPCNC Nano Estlcam Shield.kicad_pcb, MPCNC Nano Estlcam Shield.sch]
2019-04-18 Update
    Kleine ungenauigkeit an den Befestigungslöchern der Frontplatte korrigiert.
2019-04-18 Add files via upload
    Korrigierte Versionen
    [Frontplatte-Blanko-korrigiert1.stl, Frontplatte-komplett-korrigiert1.stl]
2019-04-18 Delete Frontplatte-Blanko.stl
    Wegen kleinem Fehler bzw einer Ungenauigkeit gelöscht
    [Frontplatte-Blanko.stl]
2019-04-18 Delete Frontplatte-komplett.stl
    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
    [Frontplatte-komplett.stl]
2019-04-18 Delete Frontplatte-Blanko.step
    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
    [Frontplatte-Blanko.step]
2019-04-18 Delete Frontplatte-Komplett.step
    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
    [Frontplatte-Komplett.step]
2019-05-12 Added 3D models of MPCNC Estlcam Shield for CAD enclosure deisgn
    - added .step file
    - added .wrl file (includes pcb silkscreen)
2019-11-07 Gerber v1.4 created
    [MPCNC Nano Estlcam Shield-B.CrtYd.gbr, MPCNC Nano Estlcam Shield-B.Cu.gbl, MPCNC Nano Estlcam Shield-B.Fab.gbr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]
2019-11-07 Housing from Henrik Word added.
    The Housing is based on Daniel's housing.
    [Front groß.stl, Oberteil groß.stl, Rückseite groß.stl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]
2019-11-11 Create Oberteil Nano Controller Box.stl
    Same as "Oberteil groß", but the is moved a bit to the middle, to have more space between fan and GX-16.
    [Oberteil Nano Controller Box.stl]
2020-05-28 Update README.md
    Added supplier PCB/Parts (Google Forms)
2020-07-21 Firmware added for ATtiny25/45/85
    Spindle RPM-Signal to PPM-Signal conversion (e.g. for controlling RC model motor with ESCs, RC model servos, etc)
